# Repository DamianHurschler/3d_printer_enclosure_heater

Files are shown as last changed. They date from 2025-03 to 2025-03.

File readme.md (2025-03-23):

# 3d_printer_enclosure_heater

A PID controlled heater for 3d printer enclosures, providing stable and possibly elevated enclosure temperatures during printing.

* The heater uses 12V PCI-E power from a standard ATX power supply. If the power supply has had efficiency it provides extra heating - if it is inside the printer enclosure.
* The fans are always on, but the heating elements are PWM controlled at 4Hz based on a PID controller which mositors enclosure temperature.
* The temperature can be adjusted in 1°C increments with buttons.
* The heaters can be disable via a button, so only the fans are running.
* The display indicates current and set temperature and PWM output from 0 to 100%.

WARNING! This information is provided as-is and the author denies all liability for building or operating the described device. Only trained professionals should build the device. The device shall only be operated wile monitored by a skilled operator, never operate it unattended - there is the risk of fire, injury and death!

## Software

* The source code is locaded in `/src` and is compiled using platform.io.
* The setup is geared towards a Sparkfun `esp32things_plus` board but should work with any ESP32 - provided the pinout is adapted.
* The `main.cpp` contains all the configurable constants, most importantly the PID gains.
* The serial debugging function allows a bunch of additional things to be printer. What's enabled has been made compatible with this serial data monitor for realtime plotting: https://github.com/hacknus/serial-monitor-rust

## Hardware

* Hardware related files are under `/hardware`
* The FreeCAD file, as well as *.stl, *.3mf from Prusa Slicer as well as the *.gcode I used on my mini are in the `/hardware/3d_print_files` directory
* More photos are in `/hardware/photos`
* Pin assignments are defined in the `/src/main.cpp` file

### Parts

|count|item |
|---|---|
|1  |THING PLUS ESP32 WROOM USB-C |
|1  |SparkFun Environmental Sensor Breakout - BME680 (Qwiic) |
|1  |T-BEAM OLED-1.3" display with 3 buttons |
|1  |12V to 5V buck converter |
|3  |15A MOSFET PWM drivers |
|3  |12V 70W (in reality ~50W) heaters with fan |
|3  |KSD301 Normally Closed 10A overtemperature switches operating at 80°C  |
|12 |M4 Threaded Inserts |
|12 |M4x10mm screws |
|6  |M3 Threaded Inserts |
|6  |M3x8mm screws |
* Electrical wiring to connect all the compnents, including soldering equipment and skills
* A PCI-E cable and an ATX power supply able to provide ~200W at 12V
* 3D printer and material to produce the 3D printed parts

### Design description

* The fans, the DC-DC converter, the ESP32, the sensor and the display get continuous power.
* The ESP32 uses the BME680 sensor readings to determine temperature and by PID algorithms will regulate the pulse width of a PWM output.
* The 12V power for the heaters first passes thru the overtemperature switches. These switches would cut power at 80°C. In case a fan fails or similar deficiencies it will take some time, but then the overtemp switches will disable the heaters. This has been confirmed thru testing and thermal imaging was used for optimal placement of the thermal switches. However - never run the heater unattended!
* Then the voltage is fed to the three MOSFETs (one per heater) which are switching the heaters on and off at a rate of 4Hz (the lowest the ESP32 allows) and will modulate the on-time as dictated by the PWM output of the ESP32. This provides fine grained control over the amount of heat added to the chamber.
* When the device gets power the ESP32 will start up and the display will show the current temperature and the default set_point at startup. The PWM output will be disabled and the display will show 'OFF'.
* The operator can then adjust the temperature with the '+' and '-' buttons, and enable the heater with the center button.
* Now the diplay will show 'ON' and the heaters are getting the required amount of power to reach the desired temperature.
* During operation the target temperature can be changed, or the heaters disabled by again pusing the center button.

### Failure modes and mitigations - safety

* One of the MOSFETs could fail closed and permanently provide power to a heater, causing overheating.
    * Since the fans continuously get power, there should be no overheating of any sort. There would only be issues with incorrect temperatures.
* A fan could fail while the heater still gets power, leading to overheating of some sort.
    * The heaters are PTC resistive heater elements. With increasing temperature their resistance increases, which will reduce current and thus power of the heater. At some point radiation and convection and residual heater power reach equilibrium and further increases in temperature are stopped. Thermal imaging confirmed this to take the heater element to 200 to 250°C and the exterior of the heater case well beyond 100°C. While this may be no issue, there is still the risk that something could start melding and a fire could start.
    * Thermal imaging was used to determine the location on the exterior of the heater case where temperature rises first and where its the highest. In this location thermal switches were placed. They will see 80°C and disable power to the heater before the heating element reaches 200°C and should therefore prevent the worst.
    * However, the thernal switch will reset itself once the temperature as gone back down, and the heater with the failed fan would turn on again. Safety could be increased by using a single-use thermal fuse...
* A wire could cause a short circuit and wires could burn. And there are no fuses in the desing to prevent it.
    * On the PCI-E ATX power supply side, this is no different to any normal PC. The power supply should detect shorts and disable the output. Make sure to use wires equal or larger cross section than what comes from the power supply.
    * On the 5V side the DC-DC convertwer should be the limiting factor which would fail or disable power. Small fuses should be introduced to provide better safeguards against this failure.



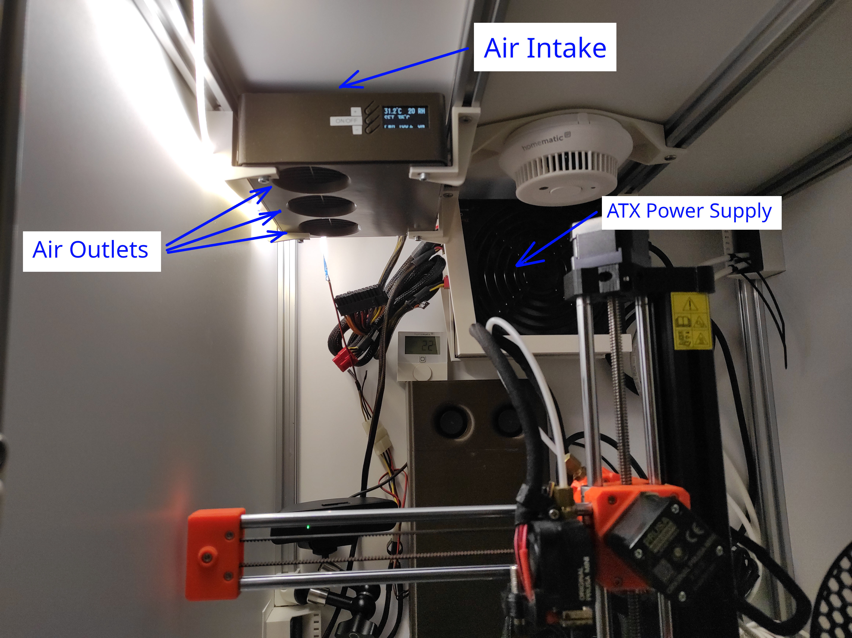
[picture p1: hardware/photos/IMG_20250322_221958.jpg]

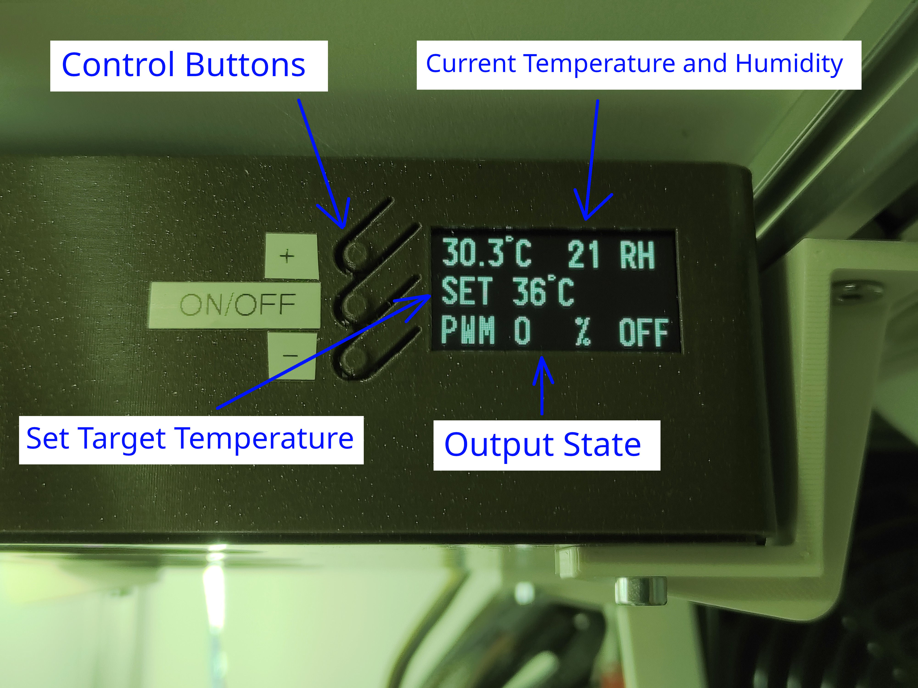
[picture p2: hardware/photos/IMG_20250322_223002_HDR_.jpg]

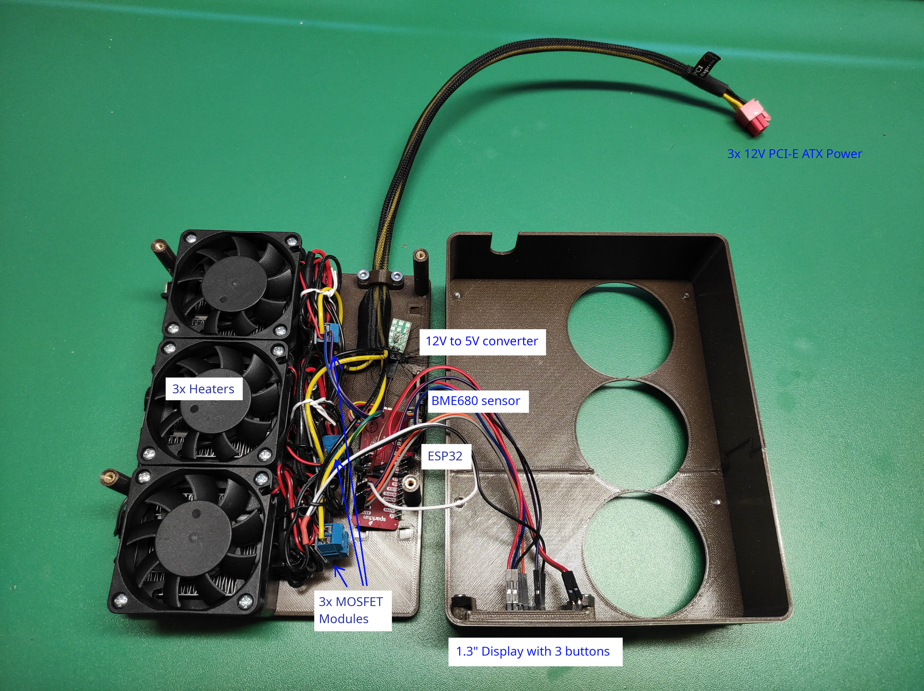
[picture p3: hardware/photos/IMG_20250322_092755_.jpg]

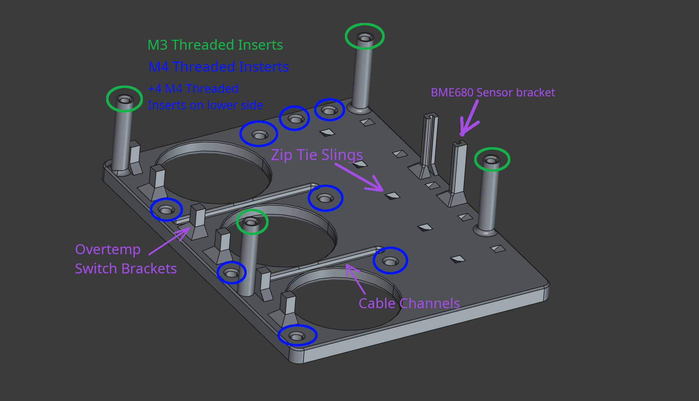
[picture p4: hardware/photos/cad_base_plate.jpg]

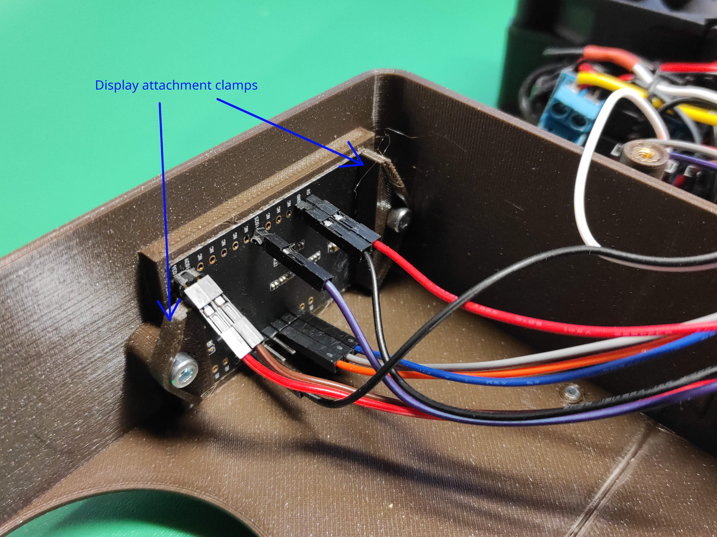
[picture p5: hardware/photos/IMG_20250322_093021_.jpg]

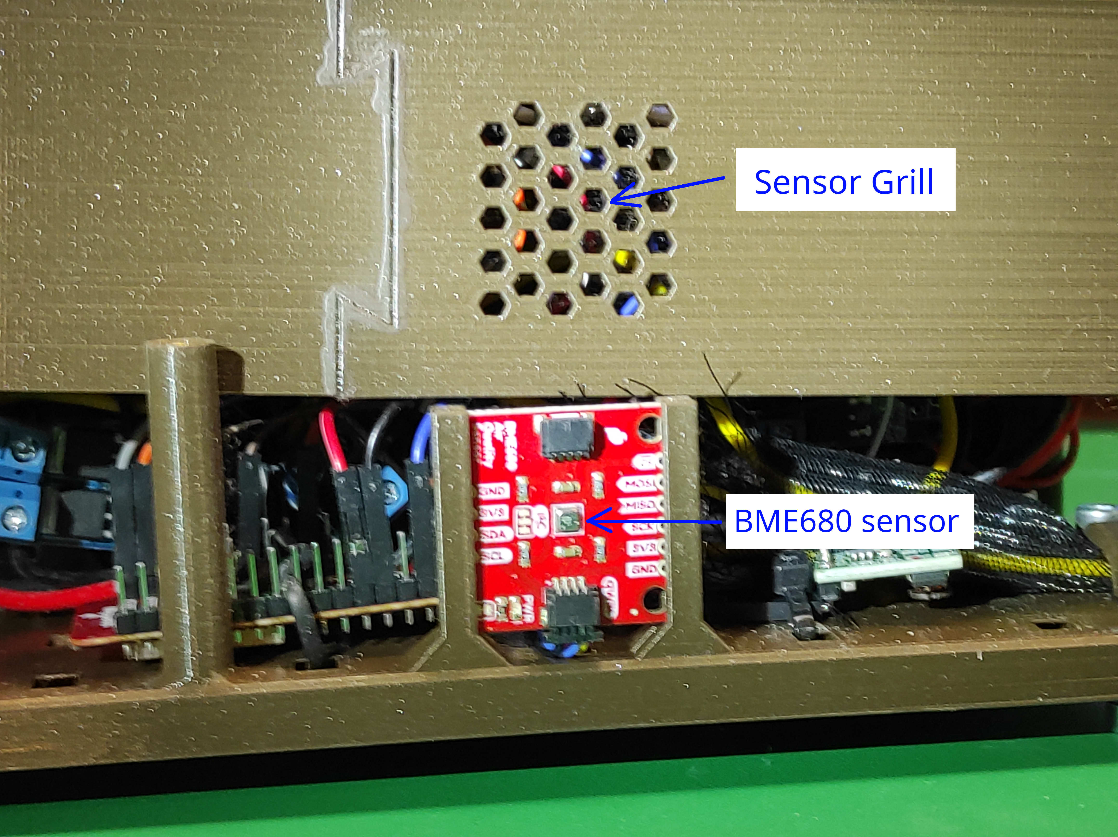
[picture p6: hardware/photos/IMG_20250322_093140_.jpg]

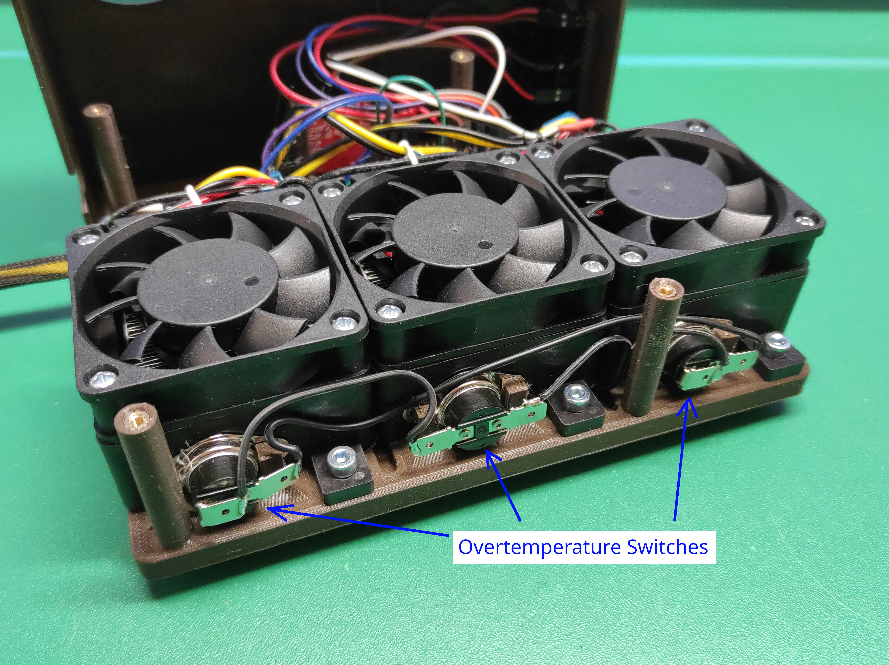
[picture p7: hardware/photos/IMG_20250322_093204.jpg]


## Why?

My shop is not heated and gets below 10°C during winter. This causes two problems:
* The Prusa mini will throw an error and reboot - preventing printing - whenever the nozzle or bed temperatures read below 10°C, because this trips some sofware monitors who flag the readings as 'outside a valid range'.
* Even PLA warps significantly at these ambient temperatures. This led me to build an enclosure, but because the enclosure temperature fluctuated depending on print activity and material, the results were still inconsistent.

The actively heated enclosure pre-warms the filament, provides a dry environment, stable temperatures with consistent results and elevated temperatures beyond 40°C which also makes printing ASA on the mini easy. I have yet to test PC and similar advanced materials.

## Notes

The Prusa mini is limited to 180mm (maybe 183 if you relally push it), which means I had to print the lid in two parts. This gave me the ugly sceam. Don't do that if you don't have to!

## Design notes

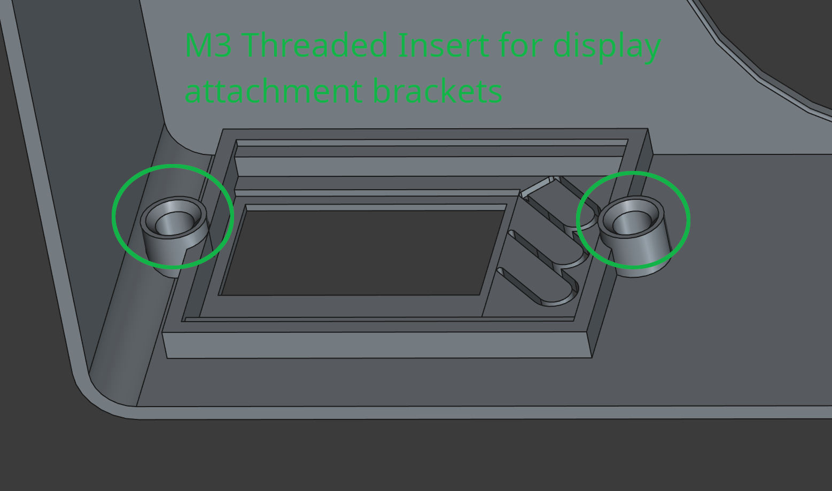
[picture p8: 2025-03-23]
hardware/photos/cad_display_bracket.jpg

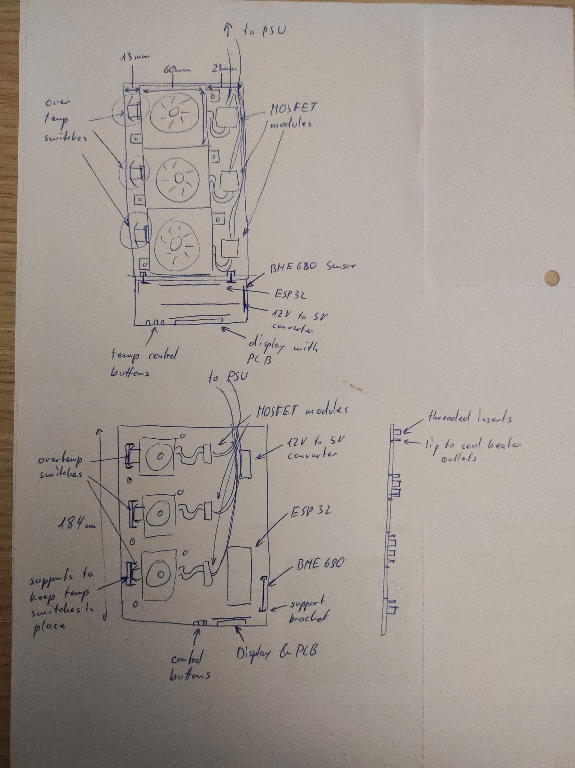
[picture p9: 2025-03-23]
hardware/photos/enclosure design sketch.jpg

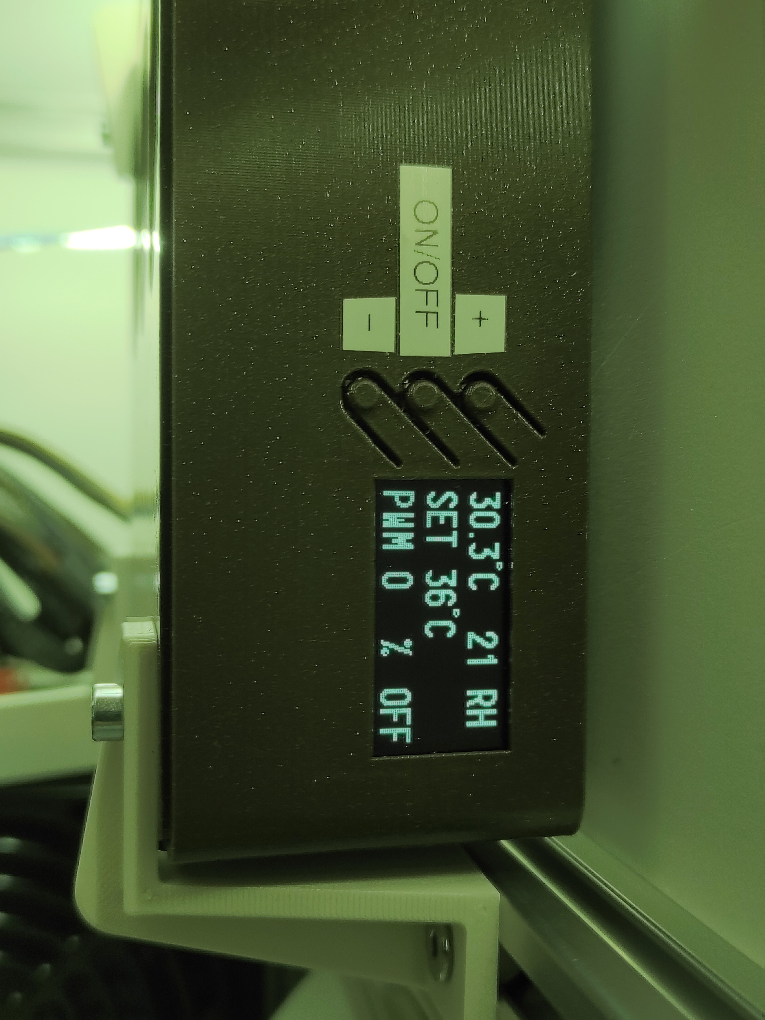
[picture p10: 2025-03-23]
hardware/photos/IMG_20250322_223002_HDR.jpg

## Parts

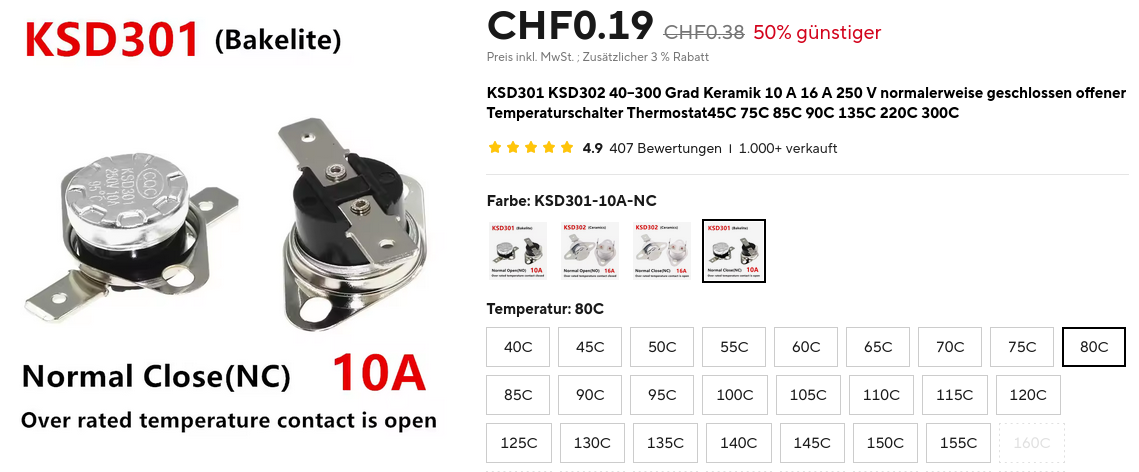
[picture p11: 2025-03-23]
hardware/components/temp switch normally closed, 10A, 80C.png

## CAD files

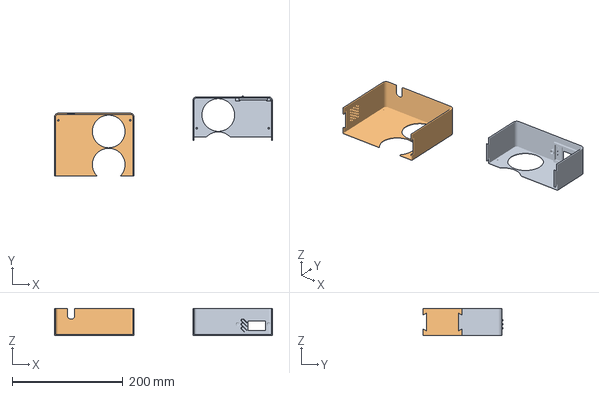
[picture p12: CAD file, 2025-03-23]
hardware/3d_print_files/heater_enclosure-heater_enclosurebottom_lid.3mf
394.2 x 143.9 x 49.0 mm
heater_enclosure-heater_enclosure_lid.stl x 2

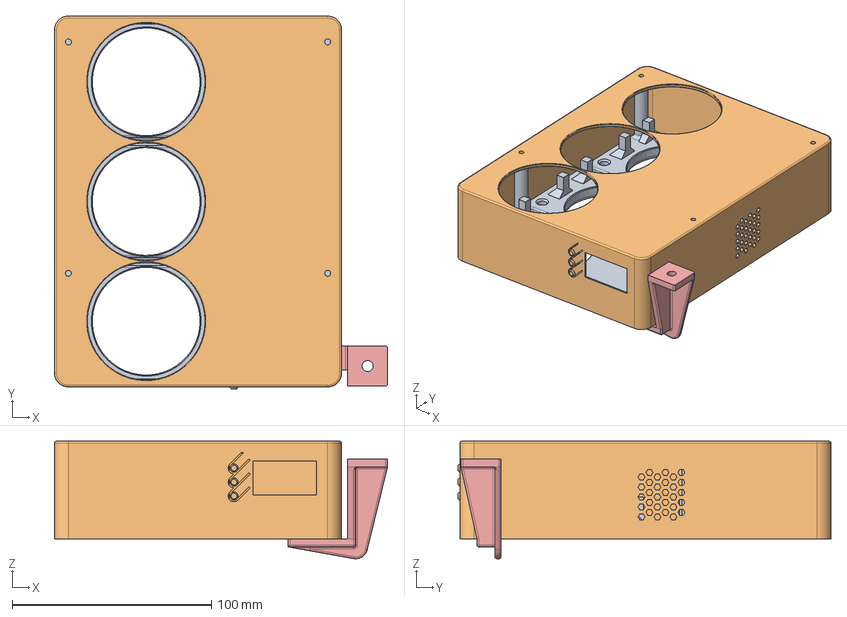
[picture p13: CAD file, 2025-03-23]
hardware/heater_enclosure.FCStd
167.0 x 187.0 x 59.0 mm
bottom_plate
lid
display_clamp
cable_clamp
mount_bracket

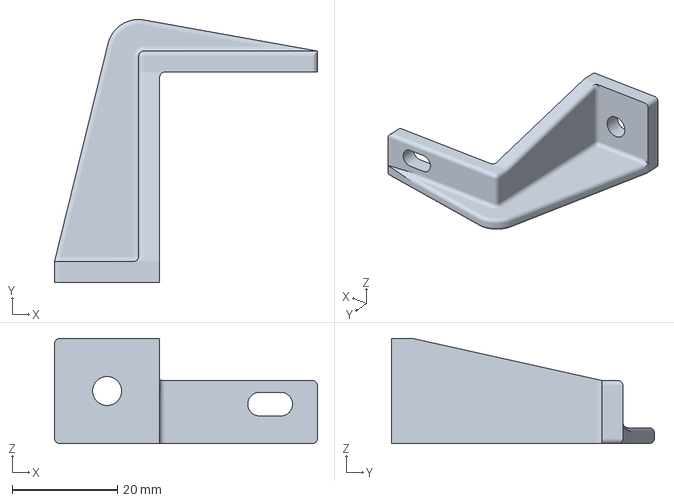
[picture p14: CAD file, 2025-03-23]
hardware/3d_print_files/heater_enclosure-heater_enclosuremount_bracket.3mf
50.0 x 50.0 x 20.0 mm

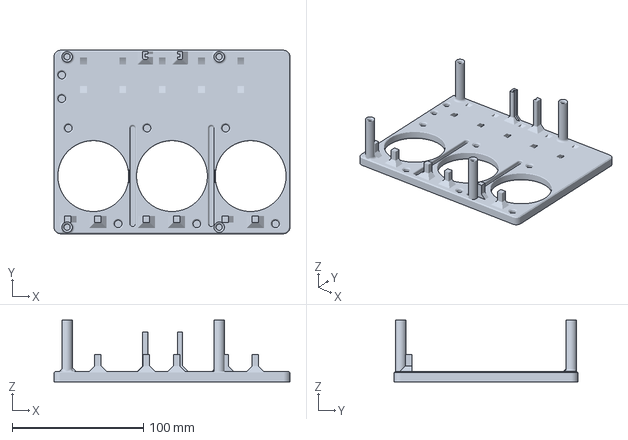
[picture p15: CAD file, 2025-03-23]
hardware/3d_print_files/heater_enclosure-heater_enclosurebottom_plate.3mf
180.0 x 140.0 x 47.0 mm

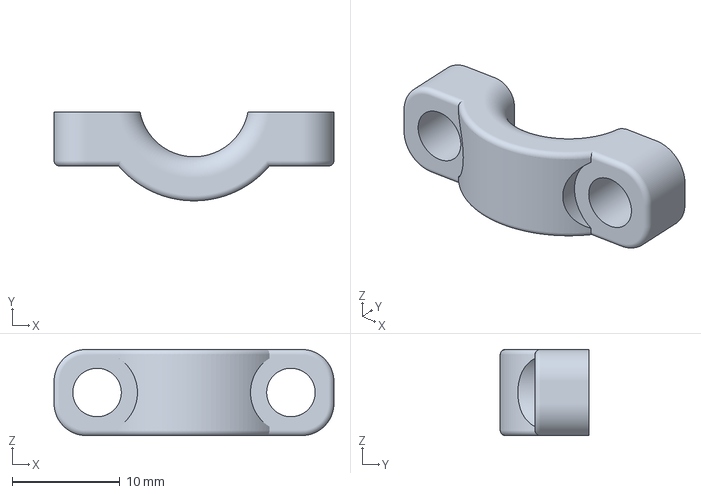
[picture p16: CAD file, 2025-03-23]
hardware/3d_print_files/heater_enclosure-heater_enclosurecable_clamp.3mf
26.0 x 8.24 x 8.00 mm

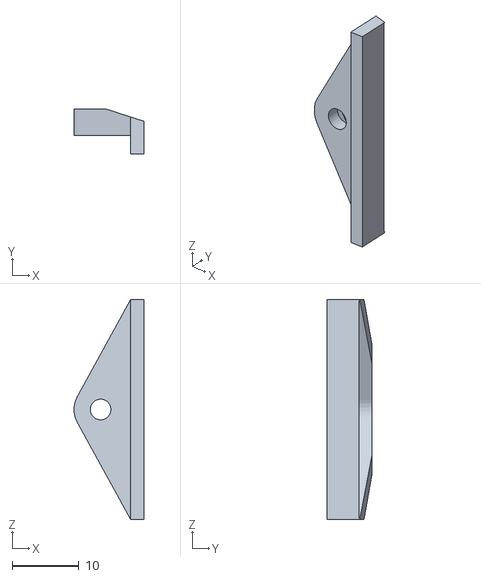
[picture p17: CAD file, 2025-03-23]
hardware/3d_print_files/heater_enclosure-heater_enclosuredisplay_clamp.stl
10.5 x 6.80 x 33.0

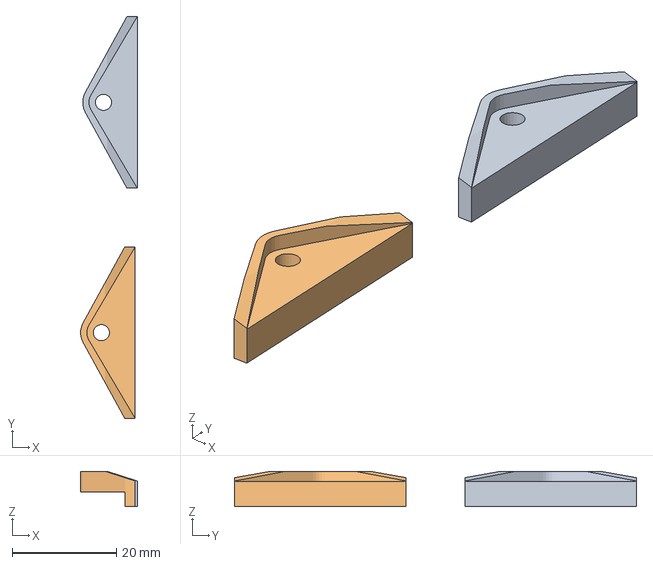
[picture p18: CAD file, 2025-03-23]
hardware/3d_print_files/heater_enclosure-heater_enclosurebottom_display_clamp.3mf
10.9 x 77.3 x 6.80 mm
heater_enclosure-heater_enclosuredisplay_clamp.stl x 2

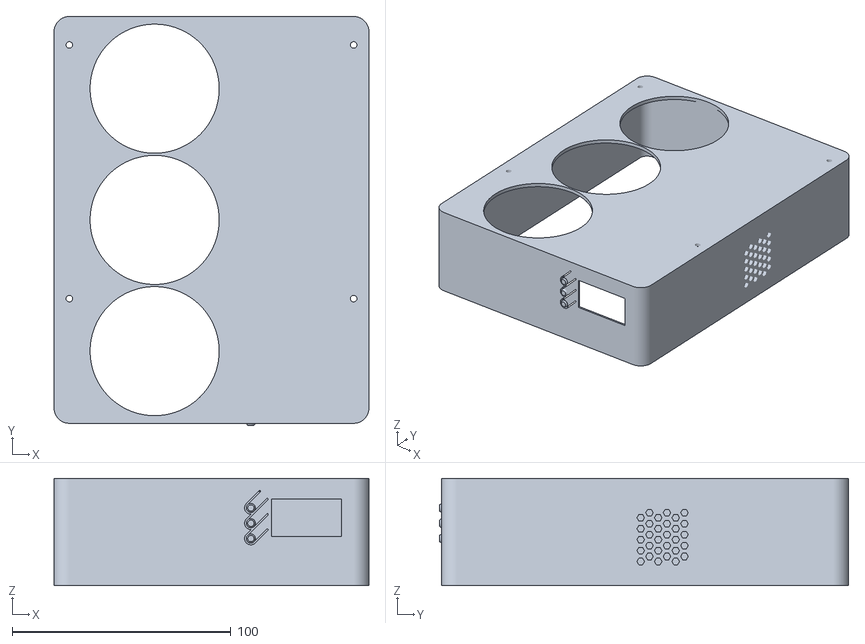
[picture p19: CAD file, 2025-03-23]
hardware/3d_print_files/heater_enclosure-heater_enclosure_lid.stl
144.0 x 187.0 x 49.0

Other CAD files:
hardware/3d_print_files/heater_enclosure-heater_enclosurecable_clamp.stl
hardware/3d_print_files/heater_enclosure-heater_enclosurelid.stl
hardware/3d_print_files/heater_enclosure-heater_enclosuremount_bracket.stl

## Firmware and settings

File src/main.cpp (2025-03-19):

#include <Arduino.h>
#include <Wire.h>
#include <Adafruit_Sensor.h>
#include <Adafruit_BME680.h>
#include <U8g2lib.h>
#include <math.h>
#include "pid.h"

// SH1106 LILYGO 1.3" T-Beam OLED display using I2C
U8G2_SH1106_128X64_NONAME_F_HW_I2C u8g2(U8G2_R0, /* reset=*/ U8X8_PIN_NONE, /* clock=*/ 22, /* data=*/ 23);
const uint8_t * display_font = u8g2_font_logisoso16_tf; // Set display font - https://github.com/olikraus/u8g2/wiki/fntlist12

// T-Beam 1.3 Inch OLED SH1106 Display Buttons
#define BUTTON_1_PIN 14 //      IO25
#define BUTTON_2_PIN 27 // (A0) IO39
#define BUTTON_3_PIN 26 //      IO36
bool button1_pressed = false;
bool button_enable_pressed = false;
bool button3_pressed = false;
int button_debounce = 300;
volatile double last_interrupt_time = 0;

// Create an instance of the BME680 sensor
Adafruit_BME680 bme; // I2C
float temp_offset = -3; // Offset to apply to sensor reading to correct temperature.

// Definitions for PID controller
#define PID_KP  40.0f
#define PID_KI  0.0002f //0.2f
#define PID_KD  0.0001f //0.1f
#define PID_INTEGRAL_MAX 70.0f
#define PID_INTEGRAL_MIN  0.0f
#define PID_OUTPUT_MAX 100.0f
#define PID_OUTPUT_MIN  0.0f
#define PID_INTERVAL_MS  1000UL
bool pid_initialised = false;
float measurement = 0.0f;
float set_point = 26.0f;
float pid_out = 0.0f;
unsigned long last_run = 0UL;

// Pass definitions to pid_data struct
pid_data pid = { PID_KP, PID_KI, PID_KD,
                PID_OUTPUT_MAX, PID_OUTPUT_MIN,
                PID_INTEGRAL_MAX, PID_INTEGRAL_MIN, 
                PID_INTERVAL_MS };

// Define PWM parameters
bool pwm_enable = false;
char output_state [4] = "OFF";  // String with 3 characters (plus one null character) to display ON or OFF
const int pwmPin = 15;          // PWM output pin number
const int pwmChannel = 0;       // PWM channel (0-15)
const int pwmFrequency = 4;     // Frequency of PWM signal in Hz, minimum is 4
const int pwmResolution = 8;    // PWM resolution in bits (8 bits gives 256 levels)
float pwm_scaling_factor = 0;   // Scaling factor to get from percent to binary
int dutyCycle_bin = 0;          // Resulting binary value for pwm




float read_sensor(){
    // Perform a measurement and confirm it's available
    if (!bme.performReading()) {
      Serial.println("Failed to perform reading :(");
    }
    bme.temperature = bme.temperature + temp_offset;
    return bme.temperature;
}




int set_output(float pid_out, bool pwm_enable){
  // Set PWM duty cycle
  // Calculate resolution based on 'pwmResolution' and scale it to 100% duty cycle
  // Example: 8bit res has 2pow8-1, i.e. 255 steps of resolution to cover 0-100% duty cycle
  pwm_scaling_factor = (pow(2, pwmResolution) -1) / 100;
  dutyCycle_bin = pwm_scaling_factor * pid_out;
  ledcWrite(pwmChannel, dutyCycle_bin); // Write to PWM pin
  return 0;
}




void serial_print(pid_data *pid){
  // Print temperature
  // Serial.print("Temperature = ");
  // Serial.print(bme.temperature);
  // Serial.println(" *C");

  // Print humidity
  // Serial.print("Humidity = ");
  // Serial.print(bme.humidity);
  // Serial.println(" %");

  // Print pressure
  // Serial.print("Pressure = ");
  // Serial.print(bme.pressure / 100.0); // Convert to hPa
  // Serial.println(" hPa");

  // Print gas resistance
  // Serial.print("Gas Resistance = ");
  // Serial.print(bme.gas_resistance / 1000.0); // Convert to KOhms
  // Serial.println(" KOhms");

  // Print PID variables
  // Optimised for plotting with https://github.com/hacknus/serial-monitor-rust
  Serial.printf("measurement, set_point, pid->proportional, pid->integral, pid->derivative, pid->pid_out\n");
  Serial.printf("%.1f,%.0f,%.1f,%.1f,%.1f,%.0f\n", measurement, set_point, pid->proportional, pid->integral, pid->derivative, pid->pid_out);
  // Serial.printf("pid->interval %u\n", pid->interval);

  // Print PWM output variables
  // Serial.printf("pwm_scaling_factor: %.2f\n", pwm_scaling_factor);
  // Serial.printf("pwm_enable %s\n", pwm_enable ? "true" : "false");
  // Serial.printf("output_state: %s\n", output_state);
  // Serial.printf("dutyCycle_bin: %u\n", dutyCycle_bin);
}




void update_display(float set_point, float pid_out){
  // Initialise variables for display test lines and parts of lines
  char line1 [16];
  char line2 [16];
  char line3_1 [16];
  char line3_2 [16];
  char line3_3 [16];

  // Convert data and text and store it in variables
  sprintf(line1, "%.1f°C  %.0f %RH", bme.temperature, bme.humidity);
  sprintf(line2, "SET %.0f°C", set_point);
  sprintf(line3_1, "PWM %.0f", pid_out);
  sprintf(line3_2, "%%");
  sprintf(line3_3, "%s", output_state);

  // Send text lines to display
  u8g2.clearBuffer(); // clear the internal memory
  u8g2.drawUTF8(0,18, line1);
  u8g2.drawUTF8(0,41, line2);
  u8g2.drawUTF8(0,64, line3_1);
  u8g2.drawUTF8(75,64, line3_2);
  u8g2.drawUTF8(100,64, line3_3);
  u8g2.sendBuffer(); // transfer internal memory to the display
}




// Interrupt functions to handle button presses
void IRAM_ATTR ISR_button1_pressed() {
	button1_pressed = true;
}

void IRAM_ATTR ISR_button_enable_pressed() {
	button_enable_pressed = true;
}

void IRAM_ATTR ISR_button3_pressed() {
	button3_pressed = true;
}




void setup() {

  // Initialise serial debug interface
  Wire.begin();
  Serial.begin(115200);

  // Set the button pins as input with internal pull-up resistors
  pinMode(BUTTON_1_PIN, INPUT_PULLUP);
  pinMode(BUTTON_2_PIN, INPUT_PULLUP);
  pinMode(BUTTON_3_PIN, INPUT_PULLUP);

  // Interrupts for button presses to call Interrupt Service Routines
  attachInterrupt(BUTTON_1_PIN, ISR_button1_pressed, FALLING);
  attachInterrupt(BUTTON_2_PIN, ISR_button_enable_pressed, FALLING);
  attachInterrupt(BUTTON_3_PIN, ISR_button3_pressed, FALLING);

  // Initialize the BME680 sensor
  if (!bme.begin()) {
    Serial.println("Could not find a valid BME680 sensor, check wiring!");
  }

  // Set up oversampling and filter initialization
  bme.setTemperatureOversampling(BME680_OS_1X);
  bme.setHumidityOversampling(BME680_OS_1X);
  bme.setPressureOversampling(BME680_OS_1X);
  bme.setIIRFilterSize(BME680_FILTER_SIZE_3);
  bme.setGasHeater(200, 50); // 200*C for 50 ms

 // Initialize the SH1106 OLED display
  u8g2.begin();

  // Configure display and send start message to the OLED
  u8g2.clearBuffer();               // clear the internal memory
  u8g2.setFont(display_font); // choose a suitable font
  u8g2.drawStr(0, 14, "Starting...");  // write something to the internal memory
  u8g2.setContrast(200);  // Maximum contrast
  u8g2.sendBuffer();                // transfer internal memory to the display

  // Configure PWM pin
  ledcSetup(pwmChannel, pwmFrequency, pwmResolution);
  ledcAttachPin(pwmPin, pwmChannel);

  // Initialise PID controller
  pid_init(&pid);
}




void loop() {
	if (button1_pressed) {
    if ((millis() - last_interrupt_time) > button_debounce){
      Serial.printf("Button 1 has been pressed\n");
      set_point = set_point + 1;
      last_interrupt_time = millis();
    }
    button1_pressed = false;
	}

  if (button_enable_pressed) {
    if ((millis() - last_interrupt_time) > button_debounce){
      Serial.printf("Enable button has been pressed\n");
      if (pwm_enable){
        pwm_enable = false;
        sprintf(output_state, "OFF");
      } else {
        pwm_enable = true;
        sprintf(output_state, "ON");
        pid_init(&pid); // Reset PID variables on reactivation of output
      }
      last_interrupt_time = millis();
    }
    button_enable_pressed = false;
	}

  if (button3_pressed) {
    if ((millis() - last_interrupt_time) > button_debounce){
      Serial.printf("Button 3 has been pressed\n");
      set_point = set_point - 1;
      last_interrupt_time = millis();
    }
    button3_pressed = false;
	}

  measurement = read_sensor();

  if (( (millis() - last_run ) > PID_INTERVAL_MS) & ( pwm_enable )) {
    pid_out = pid_update(&pid, set_point, measurement);
    last_run = millis();
  }

  if (!pwm_enable) {
    pid_out = 0;
  } 

  set_output(pid_out, pwm_enable);

  serial_print(&pid);

  update_display(set_point, pid_out);
}

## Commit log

2025-02-22 Removed I2C scanner and implemented button interrupts.
2025-02-22 Added missing if statement for 3rd button press.
    [main.cpp]
2025-02-22 Added display of sensor values.
2025-02-23 Corrected display data pin, while strangely the display worked before and after the change without issues.
    [main.cpp]
2025-02-23 Simplified temperature reading and run it in sepparate task.
2025-02-23 Further rediction in gas sensor heating, to reduce impact on temperature sensor.
2025-02-23 Introduced simple hardcoded offset to improve temperature reading accuracy.
2025-02-23 Set to read sensor data at 1 Hz.
2025-02-23 Moved button intterupt setup to the setup function.
2025-02-23 Moved serial print of debugging data to separate function.
2025-02-23 Further tuning of offset due to the board seemingly heating up.
2025-02-23 Improved font selection, improved character set to include degree circle and fixed up the display drawing process in a single print to address display flickering.
    [main.cpp]
2025-02-23 Included set point temperature for controller.
2025-02-23 Added debounce to the buttons.
2025-02-23 Relocated PWM setup.
2025-02-23 Implemented first crude and not completely tested PID control loop.
2025-02-23 Fixed display to correctly indicate negative temperatures.
    [main.cpp]
2025-02-23 Added mechanisms to prevent also negative windup.
    [main.cpp]
2025-02-24 Included variable definition, misteriously missing from the previous commit.
    [main.cpp]
2025-02-25 Implemented disabling of serial output also for sensor read operation.
2025-02-25 Improved button debounce feature and centralised debounce setting.
2025-02-25 Updated to more 'correct' integrator algorithm and improved integrator clamping.
    [main.cpp]
2025-02-25 Improved derivative control to go by measurement instead of error. Also improved float variable definitions.
    [main.cpp]
2025-02-25 Corrected variable data type.
    [main.cpp]
2025-02-25 Cleanup of proportional part of pid controller.
2025-02-25 Included disable feature for PID serial debug output.
2025-02-25 Implemented pwm output feature to control heater.
2025-02-27 Further increased integral pid clamping to allow sufficient authority. Also removed delay on main loop to restore display responsiveness.
2025-03-08 Collected all serial printing in separate autonomous function.
2025-03-08 Consolidated all serial print things in one function and removed the 'debug enable' feature, since the serial printing in this form does not impact overall performance or cycle time.
2025-03-08 Implemented the center button 2 as control button to turn heaters ON and OFF, plus all the things necessary to appropriately display the operating state.
2025-03-08 Moved code to set the pwm output pin to separate function.
2025-03-15 Moved PID control logic to separate file, generalised the PID as much as possible and got rid of separace processes to correctly call the PID with arguments.
    [main.cpp]
2025-03-19 Improved readavility of pid code, but decided that comments do not help, it's so neat!
2025-03-19 Modified serial print to optimise it for plotting on serial-monitor-rust.
2025-03-23 Added all cad files, images and expanded the readme.
    [heater_enclosure-heater_enclosure_lid.stl, heater_enclosure-heater_enclosurebottom_display_clamp.3mf, heater_enclosure-heater_enclosurebottom_lid.3mf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]
